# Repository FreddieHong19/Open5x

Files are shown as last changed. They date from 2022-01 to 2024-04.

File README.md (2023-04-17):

# Introduction

Democratising 5-axis 3D printing

At present, many people are unable to access 5-axis 3D printing due to the unavailability of hardware and software for personal use. Commercial multi-axis CNC machines and robotic arms are not designed specifically for additive manufacturing, and their firmware does not support standard 3D printing functions. Moreover, even the most affordable 5-axis machine still costs more than $9,945, which makes it prohibitively expensive for personal use. 

On the other hand, community engagement has been the primary driving force behind the widespread adoption of 3D printing in various industries. Through collaborative development, 3D printers have become more affordable, functional, and user-friendly. Similarly, 5-axis 3D printing could also benefit from the open-source community to accelerate its development and growth.

Open5x is a project that draws inspiration from open-source machines for personal fabrication. The project demonstrates how a popular off-the-shelf 3-axis 3D printer can be upgraded to 5-axis 3D printing, enabling more independent makers to take advantage of the benefits of conformal 3D printing.

The Open5x project was first showcased at the 13th Annual Conference on Human Computer Interaction Design and Research, and since then, has been demonstrated at various make fairs and 3D printing events such as 3D meetup Sweden, ERRF, and FormNext supported by Duet3D.

Related article:

https://dl.acm.org/doi/10.1145/3491101.3519782
https://doi.org/10.1016/j.addma.2023.103546

Link to the video:
https://youtu.be/x9rG15qrDIE

# Update

So far, Open5x hardware has been iterated and implemented onto various FDM 3D printers such as Prusai3, Voron and E3D's toolchanger system.
This conversion system requires some of the off-the-shelf components and 3D-printed parts. All of the necessary parts are listed in this repository.

The latest iteration of Open5X is running on E3D's toolchanger and Voron, developed by @BrendonBuilds 

-------

## License
The contents of this repository is under an MIT License, see [LICENSE.md](https://github.com/FreddieHong19/Open5x/blob/main/LICENSE) for more details.

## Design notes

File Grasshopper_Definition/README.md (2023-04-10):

# Usage

This folder contains the necessary files for using Grasshopper to create a 5-axis G-code.
Grasshopper is a visual scripting extension integrated into a popular 3D CAD software called Rhino 3D.
Unfortunately, Rhino 3D is not free software, but a 90 days fully functioning free-trial version is provided.

The grasshopper script here is still undergoing improvement and development.
The eventual goal is to migrate the system off Rhino 3D and operate somewhere free and open source. 

The current iteration of the Grasshopper script requires the below dependencies:

https://www.food4rhino.com/en/app/heteroptera : To find a centroid of a 3D geometry
https://docs.microsoft.com/en-us/dotnet/api/system.linq?view=net-6.0 : To collect max/min values in list

Rhino 3D and Grasshopper are excellent for simulating the movements of the hardware.
To simulate the movement, the 3D file of the rotary gantry (e.g. Prusa_5axis_profile_v2.3dm) needs to be uploaded inside the simulation node.

# Update

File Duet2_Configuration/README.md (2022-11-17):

For Prusa i3 MK3s 5-axis conversion Duet2 Wifi or Duet2 Ethernet can be used.
Two add extra two stepper motors for axis 'U' and 'V' Duex5 expansion board is required.
Please see the documents below for setting up the Duet2 board and Duex5 expansion for the first time.

https://docs.duet3d.com/en/How_to_guides/Getting_connected/Getting_connected_to_your_Duet

https://docs.duet3d.com/en/Duet3D_hardware/Duet_2_family/DueX2_and_DueX5

The steps-per-mm need to be adjusted depending on the gear-ratio, microstepping, stepper motor specs that you choose.
It would be advised to move the axis (especially U and V) at small incremental steps and assess that angle after.

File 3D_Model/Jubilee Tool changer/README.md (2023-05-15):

# Jubilee 3D Printer Open5x Implementation

This is a work-in-progress folder for files associated with creating an Open5X Jubilee 3D Printer. The files are provided, as-is, with no implied further support. Fabricating the module is easy but there is inherent risk with its use; collisions or other issues could cause permanent mechanical damage. Use at your own risk.

The files in this folder have been tested on a 300 mm^3 build space Jubilee 3D printer and may require modification for production systems.

# Introduction
These files are for modifying a Jubilee 3D printer to be compatible with the 5-axis build platform in the E3D_ToolChanger folder in this repo. By printing and assembling these parts, the Z-axis on a stock Jubilee can accept the existing 5-axis build platform.

# Integration Warnings
- Make sure to set tool change macros such that the tool will always clear the top of the 5-axis build platform before and after tool changes
- Collisions of the build plate and the gantry can happen during 5-axis printing. Be careful!

# Hardware Required
The below hardware is in addition to the additional hardware needed to make the 5-axis build platform specified in the E3D_Toolchanger folder

## Components to affix metal plate to z-axis couplers
(You can re-use the existing nuts and bolts below from your current Z-axis bed couplers if needed)
- 8x bolts to affix to linear rails
- 2x anti-backlash nuts for Z-axis travel
- 8x M4 heat-set inserts to affix to Z-axis bridge plate (Recommend Ultrasert ii)
- 8x M4 bolts to affix to Z-axis bridge plate
  
## Components to affix the 5-axis build platform to the Z-axis bridge plate
- 4x M4 bolts
- 4x M4 nuts

# Printed Parts
- 1x left bed coupler
- 1x right bed coupler

# Additional Parts
The below part can be ordered from sendcutsend or another laser cutting service (should be ~$35 total, shipped).

- 1x Z-axis bridge plate

# Firmware Notes
- A Duet3 with RepRap Firmware was used.
- An example config file is provided for you to adapt to your printer. Make sure to use the file as an example only to adapt to your own use case and printer setup.

# Additional Notes
- (A axis would rotate around the X-axis by convention)
- B axis rotates around the Y-axis by convention
- C axis rotates around the Z-axis by convention

# Potential Improvements for Next Revision
- Use 20x40 AL extrusion instead of laser-cut steel, add additional printed component in this design
- Explain changes to config vs. stock and add additional documentation

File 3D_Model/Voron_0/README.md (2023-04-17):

# Voron 0 Open5x Implementation

This is a work-in-progress folder for files associated with creating an Open5X Voron 0. The files are provided, as-is, with no implied further support. Fabricating the module is easy but there is inherent risk with its use; collisions or other issues could cause permanent mechanical damage. Use at your own risk.

The files included in this folder have been tested on a Voron v0.1 and may require modification for other versions.

Requires:
- Standard Open5x components
- 1 x 208mm 2GT belt
- 1 x 220mm 2GT belt
- 2 x NEMA17, 30mm body stepper motors (27mm preferred for B axis)
- 1 x 80-teeth, 2GT, 10mm bore pulley
- 1 x 10mm-diameter shaft, 70mm long
- 2 x Flanged Sleeve Bearing (McMaster 6659K118)
- 1 x 10mm Universal Mounting Hub
- M3/M4 Heat Set Inserts
- M3/M4/M5 Fasteners



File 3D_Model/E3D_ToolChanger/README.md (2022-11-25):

# E3D ToolChanger Open5x Implementation

This is a work-in-progress folder for files associated with creating an Open5X ToolChanger. The files are provided, as-is, with no implied further support. Fabricating the module is easy but there is inherent risk with its use; collisions or other issues could cause permanent mechanical damage. Use at your own risk.

The files included in this folder have been tested on an E3D Beta30 ToolChanger and may require modification for production systems.

Requires:
- Standard Open5x components
- 1 x 200mm 2GT belt
- 1 x 280mm 2GT belt
- 2 x NEMA17, 38mm body stepper motors
- 1 x 80-teeth, 2GT, 10mm bore pulley
- 1 x 10mm-diameter shaft, 72mm long
- 2 x Flanged Sleeve Bearing (McMaster 6659K118)
- 1 x 10mm Universal Mounting Hub
- M3/M4 Heat Set Inserts
- M3/M4 Fasteners

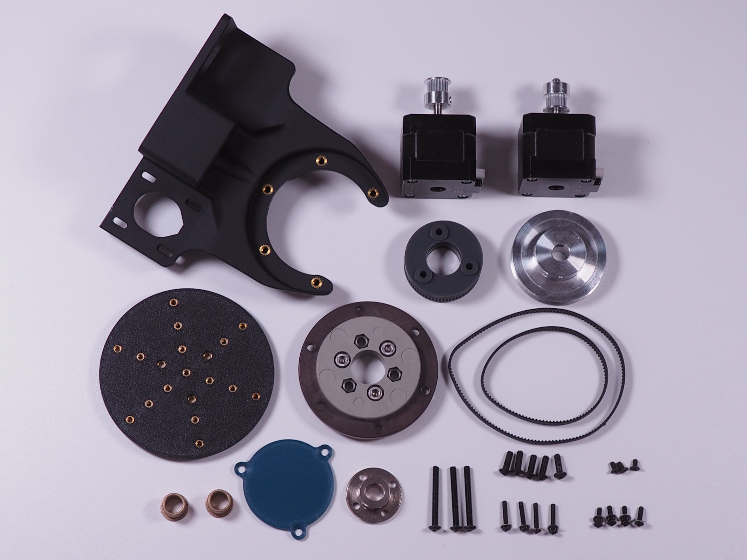
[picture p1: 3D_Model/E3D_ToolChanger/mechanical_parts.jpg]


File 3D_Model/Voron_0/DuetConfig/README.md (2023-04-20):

# These files are extremely specific to the prototype machine and should only be used as a reference.

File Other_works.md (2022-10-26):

There are several multi-axis 3D printing projects by various researchers with different approaches.
Please use pull request to add your or other project that are related

| Name  | Researcher | Link |
| ---|--|--|
| XYZdims | Rene K. Muller  | https://xyzdims.com/2021/02/08/3d-printing-penta-axis-pax-5-axis-printing-option/ |
| Aligning Material Extrusion Direction with Mechanical Stress via 5-Axis Tool Paths |Gardner et al.  | https://repository.lboro.ac.uk/articles/conference_contribution/Aligning_material_extrusion_direction_with_mechanical_stress_via_5-axis_tool_paths/9339410 |
| Reinforced FDM: Multi-Axis Filament Alignment with Controlled Anisotropic Strength | Fang et al.  | https://dl.acm.org/doi/abs/10.1145/3414685.3417834 |
| Five-axis additive manufacturing of freeform models through buildup of transition layers | Isa et al. | https://www.sciencedirect.com/science/article/pii/S0278612518301419?via%3Dihub |
|Marlin2ForPipetBot | HendrickJan | https://github.com/DerAndere1/Marlin/tree/Marlin2ForPipetBot/config/examples/multi_axis_3D_printer/HendrikJan-5D|

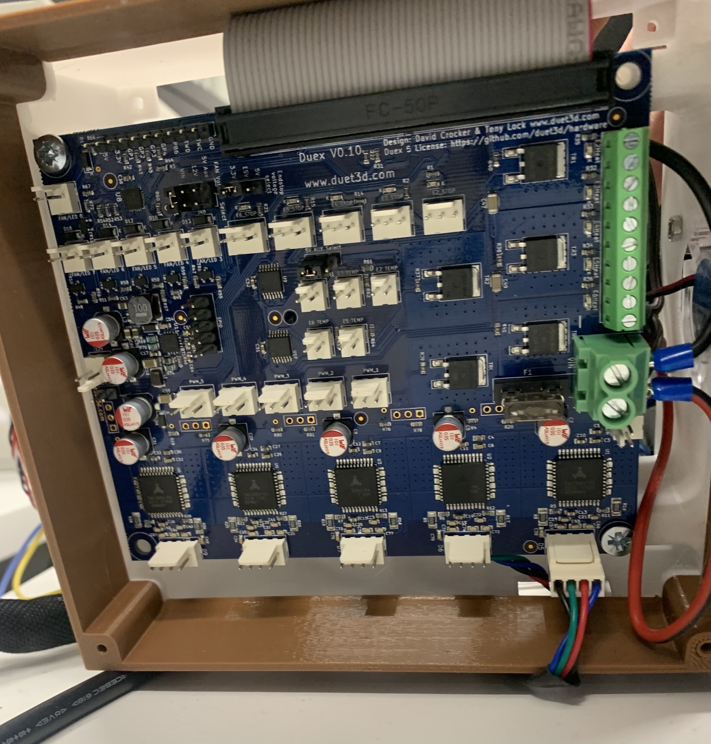
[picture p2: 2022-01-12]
images/Duex5.jpg

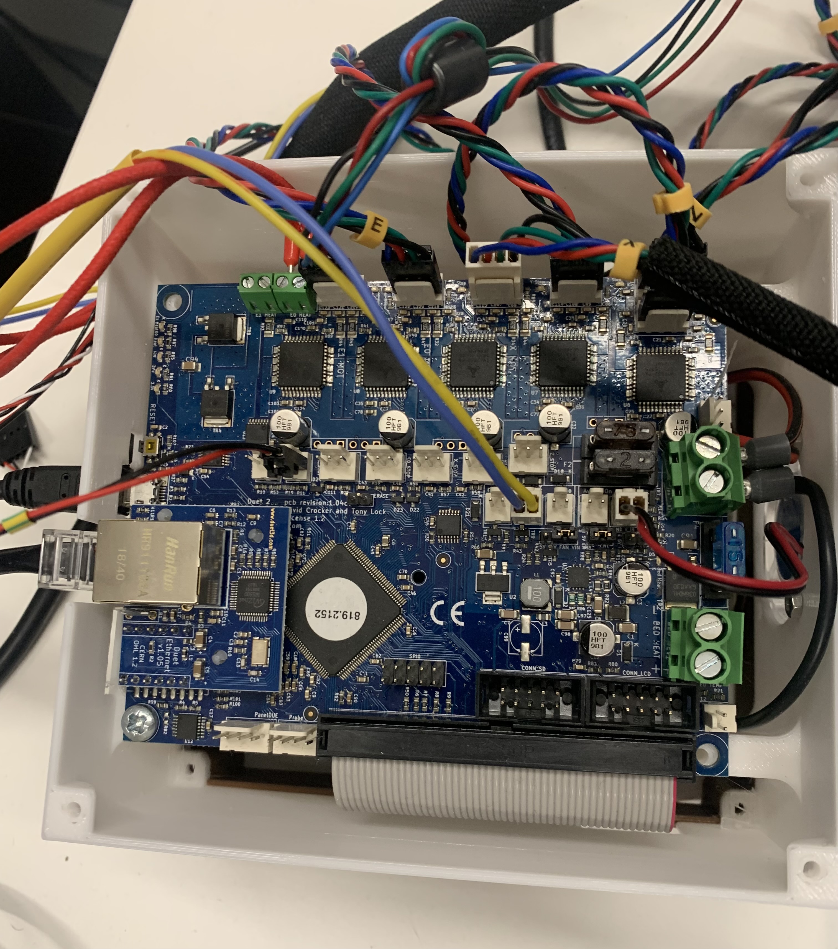
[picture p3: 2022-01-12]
images/Duet2.jpg

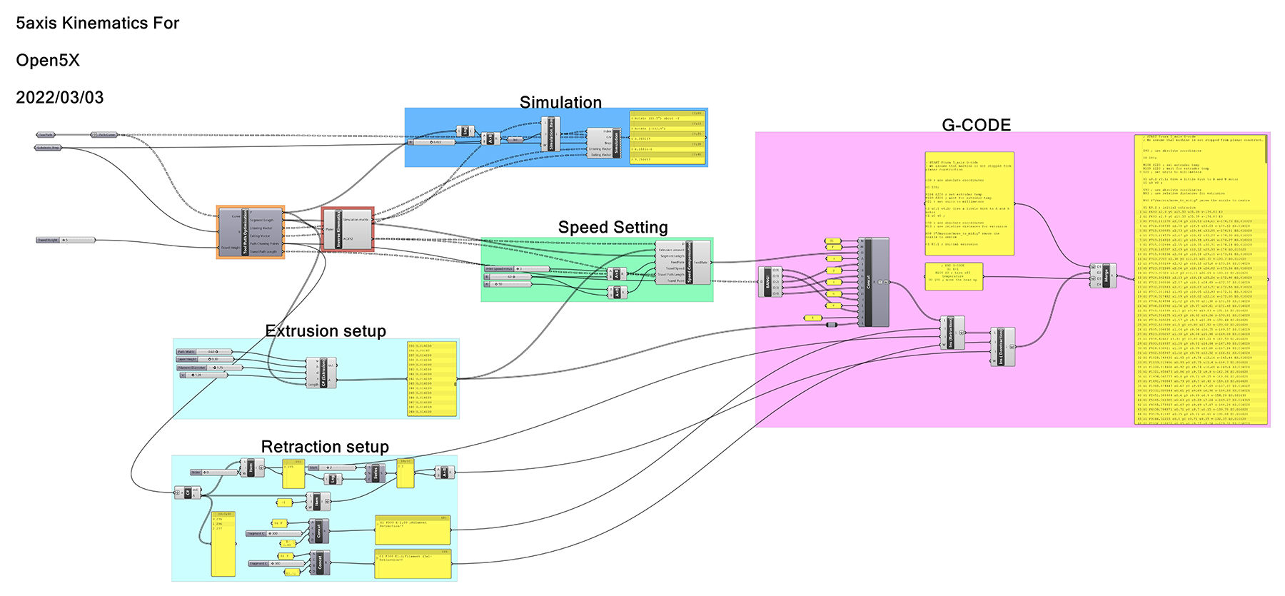
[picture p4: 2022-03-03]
images/grasshoper_main.jpg

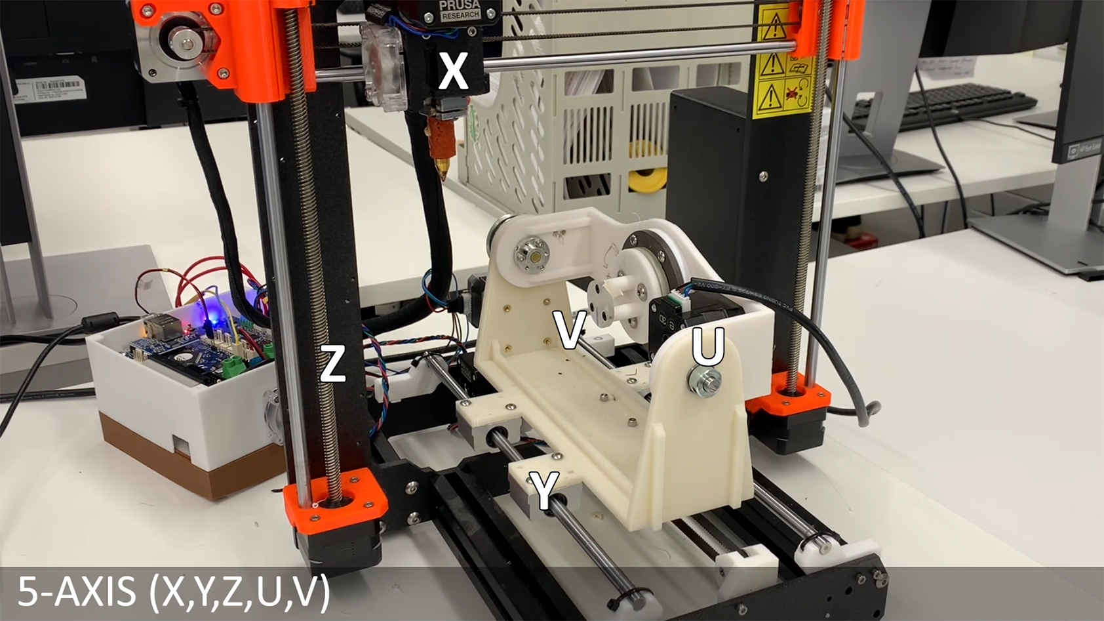
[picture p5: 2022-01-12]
images/5_axis_Prusa.jpg

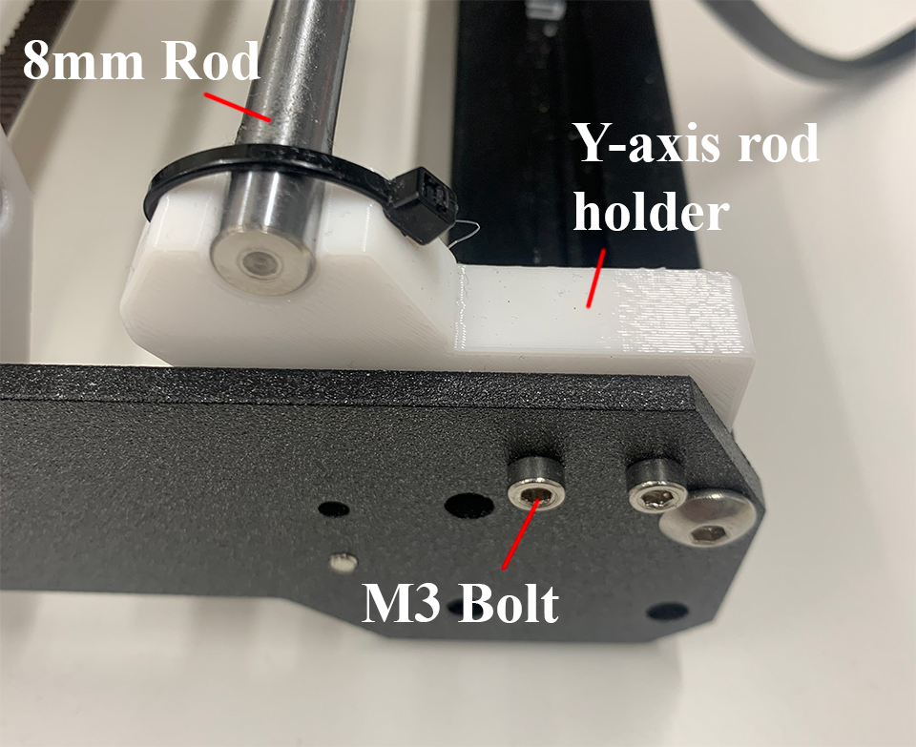
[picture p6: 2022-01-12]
images/Y_axis_rod.jpg

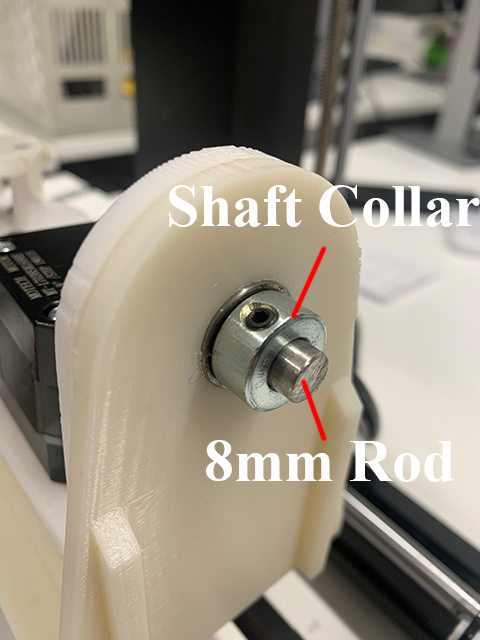
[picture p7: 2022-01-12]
images/U_axis_shaft.jpg

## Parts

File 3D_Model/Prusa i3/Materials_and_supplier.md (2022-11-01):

This a list of materials and suppliers used for converting Prusa i3 to 5-axis 3D printer

| Name  | Supplier | Link |
| ---|--|--|
| 0.9 deg NEMA 17 Compact Stepper Motor x 2 | E3D, UK  | https://e3d-online.com/products/motors |
| GT2 60 Pulley x2 8mm bore  | RepRap World, UK  | https://reprapworld.co.uk/ |
| GT2 20 Pulley x2 5mm bore for stepper motor shaft | RepRap World, UK | https://reprapworld.co.uk/ |
| 200-GT2 Belt x1 | Amazon, UK | www.amazon.co.uk/ |
| 224-GT2 Belt x1 | Odroid, UK | https://www.odroid.co.uk/index.php?route=product/product&product_id=902&search=GT2 |
| D:8mm L:35mm  Steel dowel x2 | Amazon, UK | www.amazon.co.uk/ |
| 8mm Flange Bearing x2 F6882RS | SimplyBearings, UK | https://simplybearings.co.uk/shop/ |
| 8mm shaft collar | RS Online, UK | https://uk.rs-online.com/web/ |
| Linear Bearing Slider Blocks SC8UU | Ooznest, UK | https://ooznest.co.uk/product/linear-bearing-slider-blocks/ |
| Slewing ring bearing | Igus, UK | https://www.igus.co.uk/product/661?artNr=PRT-02-20-LC |
| Duet 3 Mini 5+ | Duet3D, UK | https://duet3d.com/duet3mini5plus |
| Duet 3 Mini 2+ | Duet3D, UK | https://duet3d.com/duet3expansionmini2plus|
| (alternative to mini 5+) Duet2 Wifi | Duet3D, UK | https://www.duet3d.com/DuetWifi |
| (alternative with Duet 2 Wifi) Duex5 | Duet3D , UK | https://www.duet3d.com/Duex5 |
| Universal 8mm Pololu mounting hub| PIMORONI , UK | https://shop.pimoroni.com/ |
| Long Brass Nozzle 0.4mm | nonplanar.xyz, CANADA | https://www.nonplanar.xyz/product-page/0-4mm-non-planar-nozzle |
| M3_8mm Hex Bolt x14 (Polou mounting hub, Nema motors)| Accu, UK | www.accu.co.uk |
| M3_12mm Hex Bolt x2 (Y-axis Belt_holder)| Accu, UK | www.accu.co.uk |
| M4_14mm flat Bolt x8 (SC8UU)| Accu, UK | www.accu.co.uk |
| M4_20mm flat Bolt x8 (slewing ring)| Accu, UK | www.accu.co.uk |
| M5_25mm flat Bolt x3 (slewing ring)| Accu, UK | www.accu.co.uk |
| M3_lock nut x2 (Y-axis Belt_holder | Accu, UK | www.accu.co.uk |
| M5 nut x3 (slewing ring) | Accu, UK | www.accu.co.uk |
| M4 nut x8 (slewing ring) | Accu, UK | www.accu.co.uk |
| M3x4x5 Threaded inserts x10| Amazon, UK | www.amazon.co.uk |

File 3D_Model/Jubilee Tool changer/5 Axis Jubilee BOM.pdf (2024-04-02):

# 5 Axis Jubilee BOM

## Tools:

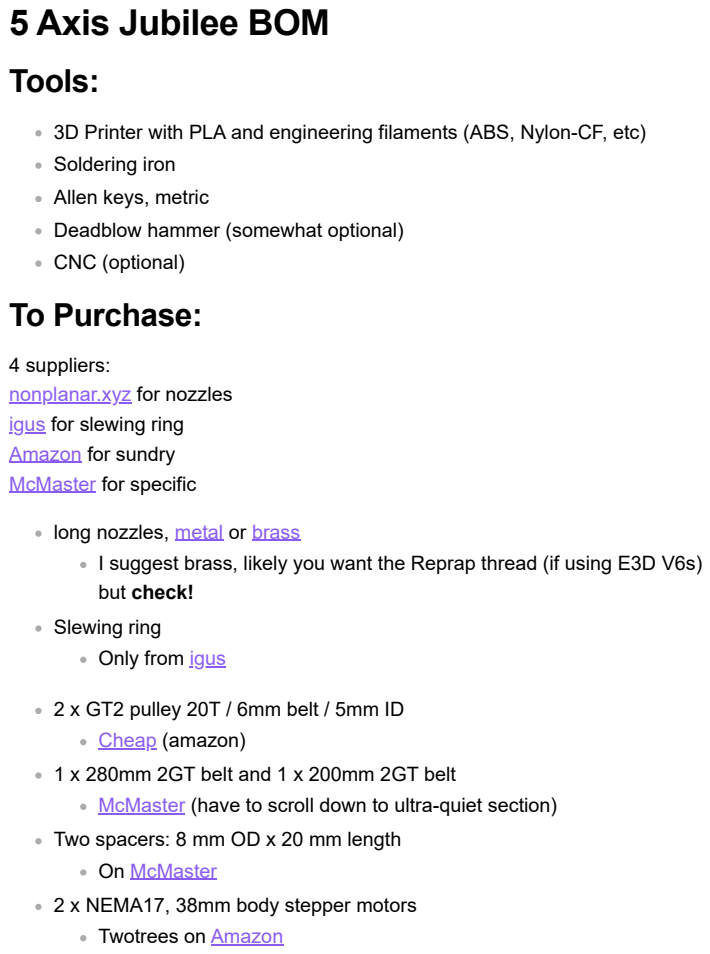
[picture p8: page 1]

3D Printer with PLA and engineering filaments (ABS, Nylon-CF, etc)
Soldering iron
Allen keys, metric
Deadblow hammer (somewhat optional)
CNC (optional)
To Purchase:

4 suppliers:
nonplanar.xyz for nozzles
igus (https://www.igus.com/) for slewing ring
Amazon (https://www.amazon.com/) for sundry
McMaster (https://www.mcmaster.com/) for specific

long nozzles, metal (https://www.nonplanar.xyz/product-page/5-all-metal-nozzle-0-4mm) or brass (https://www.nonplanar.xyz/product-page/5-reprap-brass-nozzle-0-4mm)
I suggest brass, likely you want the Reprap thread (if using E3D V6s)
but check!
Slewing ring
Only from igus (https://www.igus.com/product/661?artNr=PRT-02-20-LC)

2 x GT2 pulley 20T / 6mm belt / 5mm ID
Cheap (https://www.amazon.com/WINSINN-Aluminum-Synchronous-Timing-Printer/dp/B077GNZK3J) (amazon)
1 x 280mm 2GT belt and 1 x 200mm 2GT belt
McMaster (https://www.mcmaster.com/products/powergrip-timing-belts/) (have to scroll down to ultra-quiet section)
Two spacers: 8 mm OD x 20 mm length
On McMaster (https://www.mcmaster.com/products/spacers/spacers~/system-of-measurement~metric/od~8-000-mm/od~8-0-mm/od~8-mm/length~20-mm/screw-size~m3/)
2 x NEMA17, 38mm body stepper motors
Twotrees on Amazon (https://www.amazon.com/Twotrees-Stepper-17HS4401-Connector-Printer/dp/B07TGJT5M2)

## To Print

Print in rigid engineering filaments that can take some beating. I used Markforged ABS / Fiberglass reinforced. These parts are from Garth42's Jubilee-Open5x-assembly.step on the Open5x Github: (https://github.com/FreddieHong19/Open5x/tree/main/3D_Model/Jubilee%20Tool%20changer)

## To Machine

Can use a service like sendcutsend or cut on any CNC available to you -- it is a very simple, flat piece, and any type of metal 1/8" or thicker should do.

## Nuts and Bolts

1 x 80-teeth, 2GT, 10mm bore pulley $11.50 for 1x on Amazon (https://www.amazon.com/MECCANIXITY-Aluminium-Synchronous-Printer-Machine/dp/B0BK4VXTZC)
$17 for 2x and random stuff on Amazon (https://www.amazon.com/Befenybay-Synchronous-Aluminum-Timing-20-80T-10B-6/dp/B09YSR1TBF)
1 x 10mm-diameter shaft, 72mm long
Amazon (https://www.amazon.com/10mm-300mm-Vigorous-Hardened-Printer/dp/B0BZQ7T7JJ)
2 x Flanged Sleeve Bearing (McMaster 6659K118) Link (https://www.mcmaster.com/catalog/129/1412/6659K118)
1 x 10mm Universal Mounting Hub
- $10 but more reviews here (https://www.amazon.com/Coupling-Connector-Coupler-Accessory-Fittings/dp/B08334DK91)
- $6.50 but less reviews here (https://www.amazon.com/Cionyce-Coupling-Support-Hardness-Connector/dp/B0B63PGGZR)
Budget: parts about should run about $175. Depending on the cost of machining and which filament used in printing, below $300 is reasonable.

Main body
100 mm bed
1x left bed coupler
1x right bed coupler
Wiring holder
72T shorter c-gear (can be printed in SLA)

Z-axis bridge plate


(from Brendon Build's mechanical-parts.jpg (https://github.com/FreddieHong19/Open5x/tree/main/3D_Model/E3D_ToolChanger) on the Open5x Github)

8x bolts to affix to linear rails (M3 I think) 8x M4 bolts to affix to Z-axis bridge plate 4x M4 bolts
4x M4 nuts
M3/M4 Heat Set Inserts
M3/M4 Fasteners

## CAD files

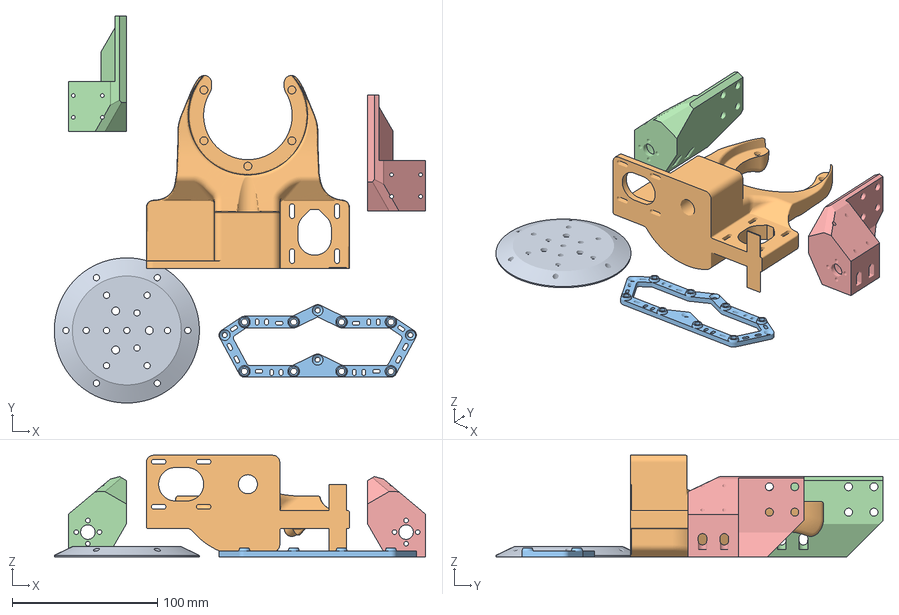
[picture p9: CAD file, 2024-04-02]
3D_Model/Jubilee Tool changer/Open5x Assembly Oriented Print Parts.3mf
256.0 x 266.7 x 70.0 mm
100mm-bed v3.step
Jubilee-Open5x-assembly_1
Tool Board Holder.step
Left Bed Coupler (Jubilee).STL
Right Bed Coupler (Jubilee).STL

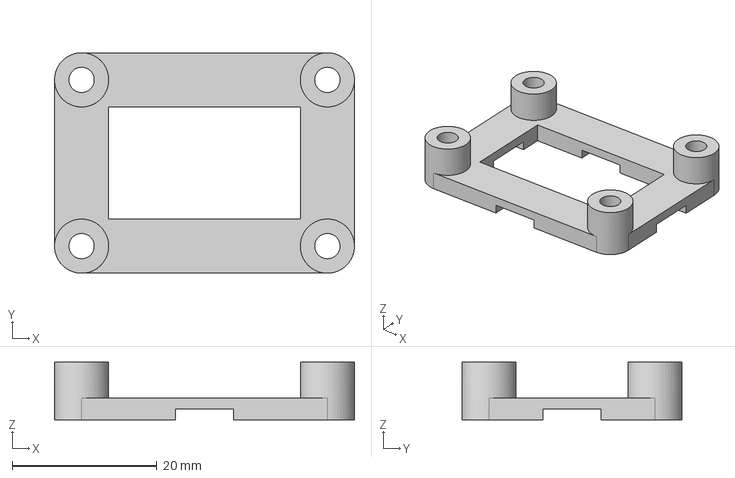
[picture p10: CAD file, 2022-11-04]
3D_Model/modifications/toolboard_23mm_bracket.step
41.5 x 30.5 x 8.00 mm

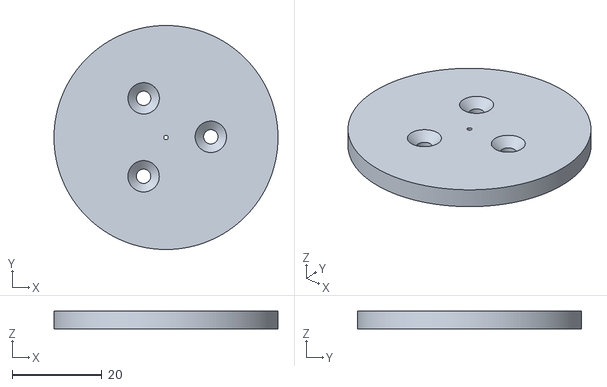
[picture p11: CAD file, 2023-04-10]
3D_Model/Prusa i3/Printbed_50mm v1.stl
50.0 x 50.0 x 4.00

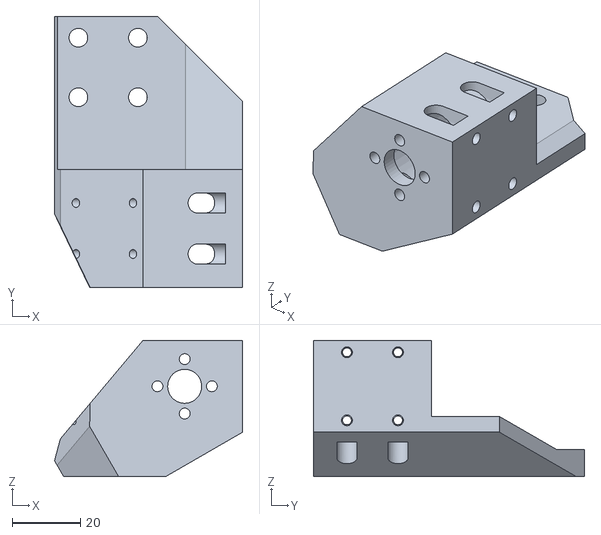
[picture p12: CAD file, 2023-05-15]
3D_Model/Jubilee Tool changer/Right Bed Coupler.STL
55.3 x 79.7 x 40.0

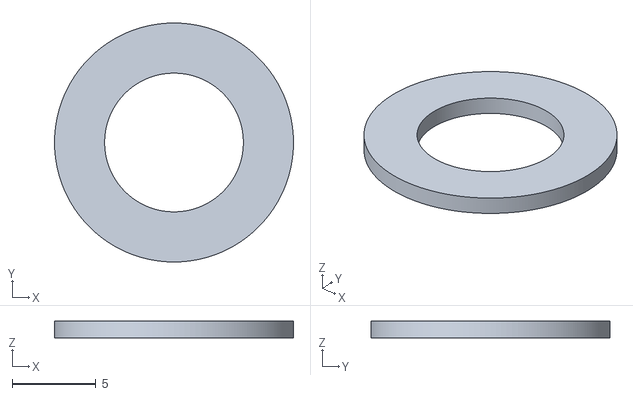
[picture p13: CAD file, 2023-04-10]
3D_Model/Prusa i3/U-axis_1mm_spacer.stl
14.3 x 14.3 x 1.00

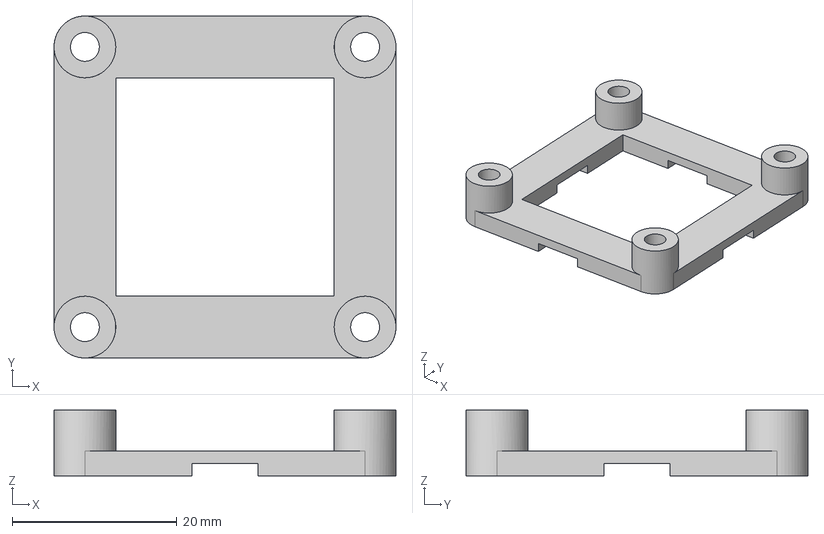
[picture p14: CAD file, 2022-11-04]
3D_Model/modifications/toolboard_34mm_bracket.step
41.5 x 41.5 x 8.00 mm

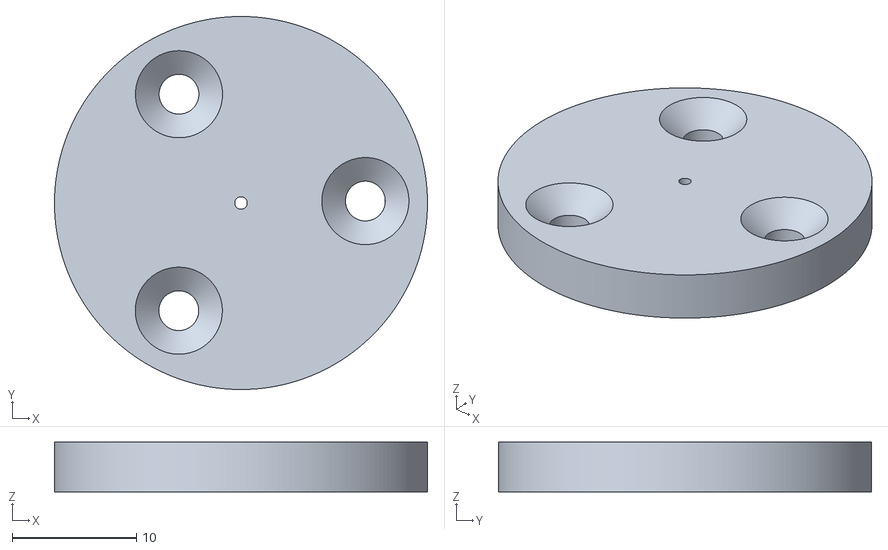
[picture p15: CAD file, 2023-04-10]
3D_Model/Prusa i3/Printbed_30mm v3.stl
30.0 x 30.0 x 4.00

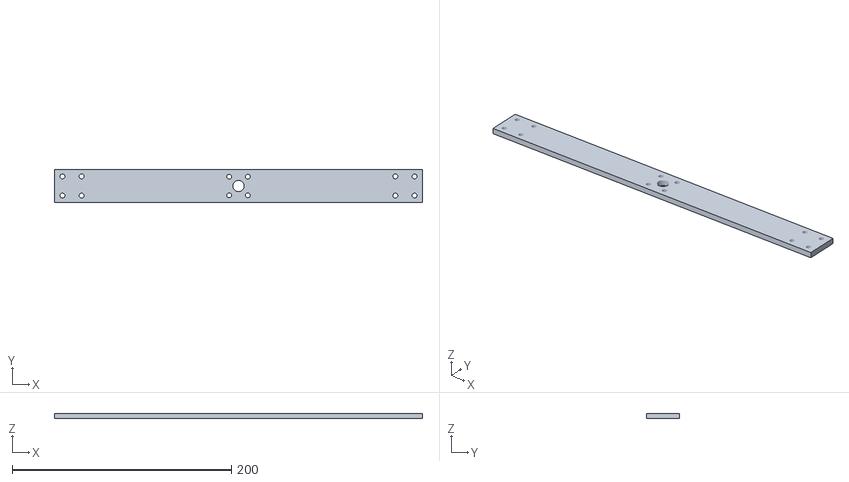
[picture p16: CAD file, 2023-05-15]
3D_Model/Jubilee Tool changer/Z-axis Bridge Plate.STL
336.0 x 30.0 x 5.00

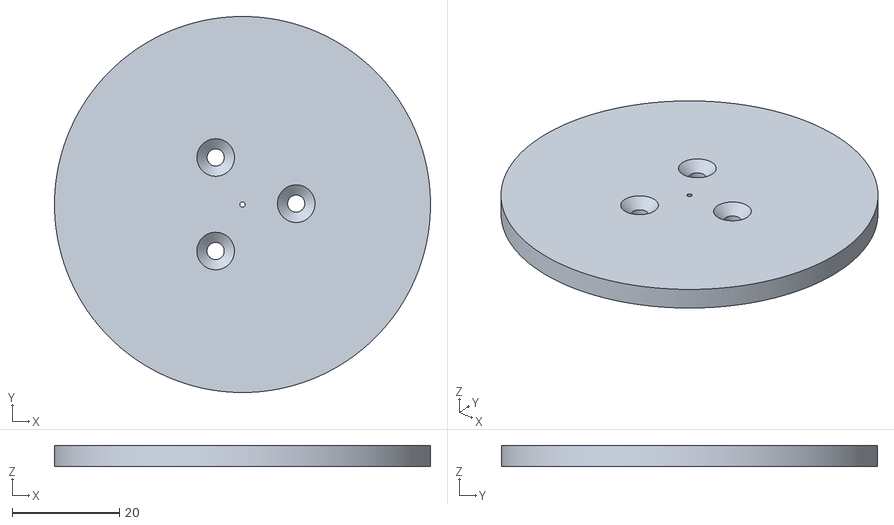
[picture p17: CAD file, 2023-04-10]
3D_Model/Prusa i3/Printbed_70mm v3.stl
70.0 x 70.0 x 4.00

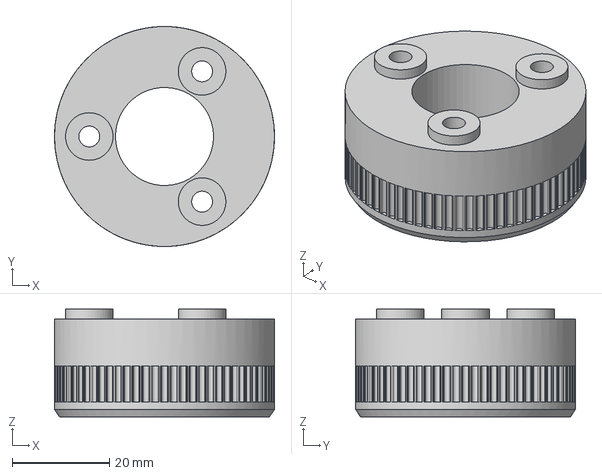
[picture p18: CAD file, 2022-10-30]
3D_Model/modifications/V_axis_pulley_72t_resin.step
45.3 x 45.3 x 22.2 mm

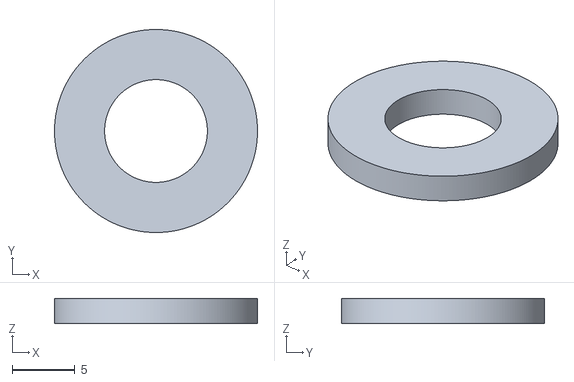
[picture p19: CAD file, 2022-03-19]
3D_Model/Prusa i3/U_axis_2mm_spacer.stl
16.2 x 16.2 x 2.00

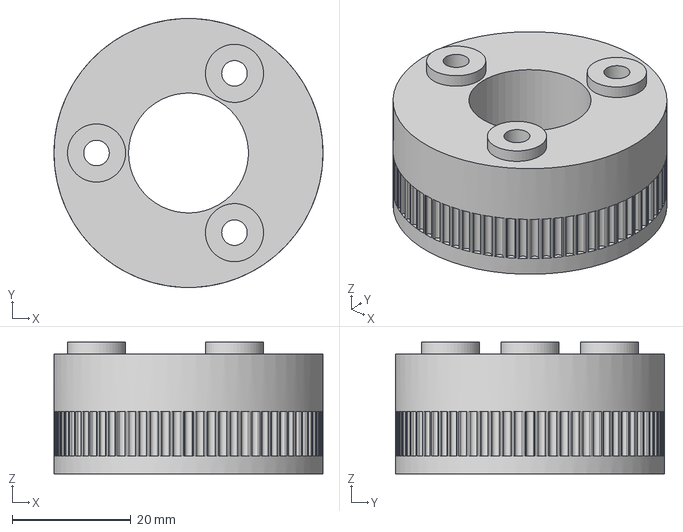
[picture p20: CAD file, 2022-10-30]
3D_Model/modifications/V_axis_pulley_72t_fdm.step
45.3 x 45.3 x 22.2 mm

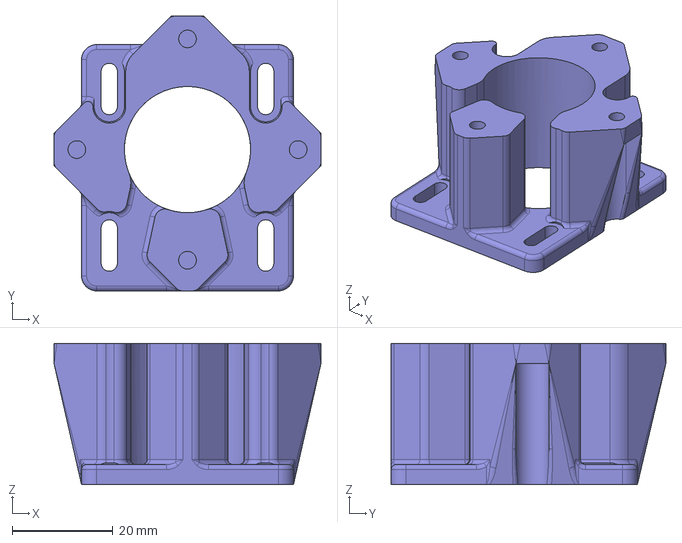
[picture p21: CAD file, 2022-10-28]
3D_Model/modifications/U_axis_motor_mount_28mm.step
52.9 x 54.4 x 28.0 mm

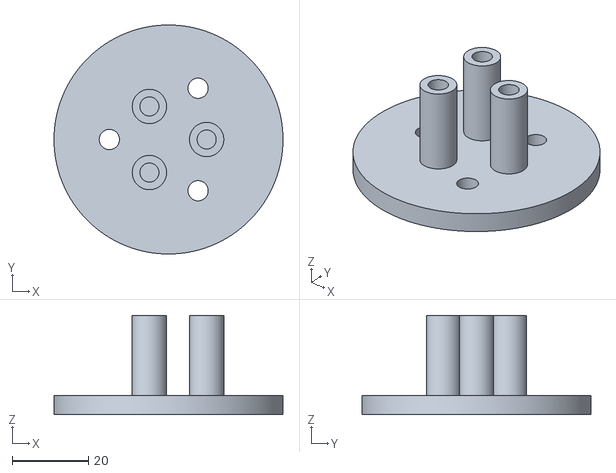
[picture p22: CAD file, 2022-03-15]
3D_Model/Prusa i3/Print_bed_support_70mm.stl
60.0 x 60.0 x 26.0

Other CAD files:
3D_Model/Jubilee Tool changer/Left Bed Coupler.STL
3D_Model/modifications/U_axis_motor_mount_22mm.step
3D_Model/Prusa i3/Y_axis_motor_mount.stl
3D_Model/Prusa i3/Y_axis_bearing_holder.stl
3D_Model/Prusa i3/Printbed_30mm v1.stl
3D_Model/Prusa i3/Slewing_ring_adaptor.stl
3D_Model/Prusa i3/U_axis_motor_mount.stl
3D_Model/Prusa i3/V_axis_carriage.stl
3D_Model/Prusa i3/V_axis_shaft_hub.stl
3D_Model/Prusa i3/Y_axis_8mm_rod_holder.stl
3D_Model/Prusa i3/Y_axis_carriage.stl
3D_Model/modifications/V_axis_carriage_4_bolt.step
3D_Model/modifications/V_axis_carriage_6_bolt.step
Grasshopper_Definition/Supportless_sample_2.3dm

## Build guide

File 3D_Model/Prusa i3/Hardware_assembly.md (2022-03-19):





Exploded Isometric image of the gantry assembly



8mm Rod fixed onto the Prusai3 frame



8mm Dowel connection on V_axis_carriage

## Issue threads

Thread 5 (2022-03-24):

Consider porting to BTT GTR

pyr0ball, 2022-03-24:
It seems TeamGloomy have gotten a decent port of RRF to work on these cheaper GTR boards. Would you be willing to consider building a version specific to that setup, or assist me in porting it?

I plan on re-engineering this project for an old FlashForge Creator Pro, and happen to have one of these GTR's on hand to work with

https://teamgloomy.github.io/gtr_pins.html

Keybored02, 2022-03-30:
I second this. The BTT GTR, SKR (with the 3axis expansion module), and Octopus are extremely widespread among makers. The Duet boards, given the cost, are more for prosumers. A Marlin port would also be a great improvement, given how 2.0.9 has simplified the addition of more (linear) axis.

FreddieHong19, 2022-03-31:
Hi,
Thank you for sharing this information about your GTR board suggestion! I will have a read through their documentation and see if it could be implemented. Personally for now, I am very satisfied with Duet board especially regarding their hardware, expandability and their web controller. I

pyr0ball, 2022-03-31:
If I had to choose between the two and price was no object, (or if I had one on hand myself) I'd probably feel the same!

Do you think if I simply used the configs from this project on the existing RRF fork for the GTR, it might just work? I'd be happy to give it a shot if so. If there's any obvious pitfalls with that method, and you could point them out ahead of time, I'd be happy to do the legwork on investigation and testing

Closed 2022-10-18.

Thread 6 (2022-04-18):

7Axis 5D Printer

HendrikJan-5D, 2022-04-18:
In response to your nice Open5x project and the question
(( We want to have more hobbyists and makers on board with 5-axis 3D printing. ))
This response.

I am new to this forum.
As a member of 3d.hcc.nl , a hobby club of members who are involved in 3d printing, 3d scanning, cad software (fusion 360).
I am involved in technical support and new developments in the 3d field.
In the context of this I have built a 5d printer
This can be done by turning and tilting the print head, or by turning and tilting the bed.
Because I couldn't choose the best method, I decoder to build both in the 3d printer, which results in a 5d printer with 7 axes.

See : https://youtu.be/pjuG15b2zaI

Further information can be found at:

My 5D printer configuration Marlin
https://github.com/DerAndere1/Marlin/tree/Marlin2ForPipetBot/config/examples/multi_axis_3D_printer/HendrikJan-5D

Wiki DerAndere1
https://github.com/DerAndere1/Marlin/wiki

Test reports 9 Axis configuration
https://github.com/DerAndere1/Marlin/issues/55

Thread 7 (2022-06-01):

Question about model slicing

Shuwrood-SSW, 2022-06-01:
Thanks for sharing your great works, but I still have no idea much about the slicing software.
For examole, when I use the model of Supportless_sample_2 (small fan), the otary bearing can't be fixed and positioned. I would appreciate a detail video tutorial  about slicing if you could.  Moreover,  can you upload the model of the spiral staircase used in your video for better. Thank you very much.

FreddieHong19, 2022-06-05:
Hi Shuwrood,

From your screenshot it appears that the model which you are importing is not at 0,0,0 coordinates. If you position the bottom face of the model, the slicing preview may appear at the right location.
I am going through iterations of development to create a stable version of the slicer +I am planning more detailed video tutorials. I am hoping to share them in a nearer time, but it is taking longer than I have anticipated!
Best,

Shuwrood-SSW, 2022-06-06:
That's really great. Looking forward to the video tutorial! Besides, could you upload the following model to github.

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

syalways, 2022-07-14:
sorry,I have a question that this model can not  print in_fill lite,is itright?

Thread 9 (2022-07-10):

How to determine the Z_Axis edge of irregular multifax surfaces

syalways, 2022-07-10:
There is a question I would like to ask, like this kind of irregular multiple surfaces how to determine which is the z-axis edge, I tried several directions, but the resulting path is not right.can you help answer it, thank you very much.
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

xuanxuanbingo, 2023-03-21:
Hello, I want to ask have you successfully reappear the whole process on the grasshopper?

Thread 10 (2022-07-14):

in_fill

syalways, 2022-07-14:
sorry,I have a question that this model can not  print in_fill lite,is it right?

FreddieHong19, 2022-10-18:
I am not too clear on what you mean. If you are referring to the auto-generating infill pattern, then the current version I am sharing is not supporting this.

Closed 2022-10-18.

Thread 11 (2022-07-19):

Help

dongqi0101, 2022-07-19:
Thanks for your work! Currently I'm trying to fork your work, but I'm having a lot of problems and really need your help.
1. Can you upload the original version of your GH (not a simplified version)
2. How did the direct printing on the sphere shown in your video work? Can the GH you upload achieve this effect?
3. I have a model here, can you help me try it? I hope to use the hemisphere as the support, and only print the pattern on the sphere. I have tried many times by myself, but all failed.
I am very interested in your work, I find it very valuable and I really need your help
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
[模型调整.zip](https://github.com/FreddieHong19/Open5x/files/9137614/default.zip)
If possible, this is my mailbox (1241153590@qq.com), looking forward to hearing from you

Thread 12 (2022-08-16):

no issue - just congrat

vivi3n, 2022-08-16:
Hello, I tested your gh code because I was so excited to understand how you created the g-code for the 5_axis machine ^^ Actually, it seems relatively (hopelessly) easy and thanks again for sharing your code and l simulation tool works so well! I will try to reproduce the Prusa too. I hope to find the time for that. Thanks again for your amazing work!

For my part I work on 3d print auxetic structure on rotative Y axis 3d printer. I hope with your project make a huge gap !

Best

Closed 2022-10-18.

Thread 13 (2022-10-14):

Can the Duet 3 mini 5+ and mini 2+ expansion board be used?

critter42, 2022-10-14:
I was looking at this project after Joel's video today and noticed I had most everything on hand to start on this. The only difference is I have the Duet 3 mini 5+ and the 2+ expansion board for it. It looks like this is all I need, since you're only using one driver on your Duet 2's expansion board. Am I correct on this?

FreddieHong19, 2022-10-18:
Hi critter42,

I believe that you are!
Your suggestion is probably a neater solution because you don't waste any extra stepper drivers!

T3P3, 2022-10-31:
yes, they are a good solution for this project!

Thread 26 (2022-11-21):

Mail

dongqi0101, 2022-11-21:
Your work is great, and I am also learning with it myself, but I have encountered many problems. Can you share your email address so that I can get your help more easily?

FreddieHong19, 2022-11-28:
Hello, Dongqi.

Could you please share the issue on repo? In case it might applies to other people who may want to use open5x?
Thank you!

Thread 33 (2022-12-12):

Make available for Mac Rhino Users

mikedattolo, 2022-12-12:
I use a mac and can not open the grasshopper file on Rhino because the plugin used to make the file is only useable on Windows machines. Is it possible to make this available in a way mac users can see and use it as well...

BigKoala33, 2022-12-14:
Hi @mikedattolo what is the name of that plugin?

BigKoala33, 2022-12-14:
Hi @mikedattolo what is the name of the plugin?

mikedattolo, 2022-12-15:
That's the problem. I'm not sure. I believe they are both Pufferfish and Heteroptera; however, I don't think it is a direct issue having to do with them. It has to do with something referenced in the grasshopper file here
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

mikedattolo, 2022-12-15:
And sorry again, I forgot that I am trying to use or make my own simulation through grasshopper to slice G-code for a 4-5 axis printer prototype I am working on for a class in college. It doesn't matter if I can't do it, but I would like to because I think this as a research subject/innovation for 3d printing would be amazing.

mikedattolo, 2022-12-16:
@BigKoala33

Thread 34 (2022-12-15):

How did you make your nozzle that long?

Page-David, 2022-12-15:
In your [video](https://www.youtube.com/watch?v=Sq2mH8-iBk8), the nozzle of hotend is obviously longer than a normal version of E3D v6 hotend. It looks like it is needed to avoid collision. So I am curious how did you make it? Is there somewhere it can be purchased?

Closed 2022-12-16.

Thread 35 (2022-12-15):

How did you make your nozzle that long?

Page-David, 2022-12-15:
In your [video](https://www.youtube.com/watch?v=Sq2mH8-iBk8), the nozzle of hotend is obviously longer than a normal version of E3D v6 hotend. It looks like it is needed to avoid collision. So I am curious how did you make it? Is there somewhere it can be purchased?

FreddieHong19, 2023-03-21:
Yes, If you check the material and supplier.md you will find the link

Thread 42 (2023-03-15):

PufferFish plugin not able to download

mikedattolo, 2023-03-15:
I try and open up the grasshopper file and I am able to download the first plugin no problem, However when it asks me to install pufferfish it fails, I have tried going to food4Rhino and manually downloading it but it doesn't acknowledge it and still asks me to download it and when I close out of the prompt I get a couple errors. At the same time I was wondering if this can be repurposed for other types of 5D printers ones that specifically uses rotational axis on the x-axis rather than the bed of the printer.

FreddieHong19, 2023-03-21:
Hi,
the grasshopper definition should still be functional without the pufferfish library. (Could you post a screenshot of an error)
The new version of the grasshoper definition will be shared soon during april!

mikedattolo, 2023-03-21:
> Hi, the grasshopper definition should still be functional without the pufferfish library. (Could you post a screenshot of an error) The new version of the grasshoper definition will be shared soon during april!

hey, thank you for responding. I figured it out. It was just because I had the pufferfish plugin block, and now it works, however I still am having issues with actually trying out the slicer, when I add in the brep and connect it to the supportless brep and substrate the slicer cant find the path curve that is connected to the conformal pathing cluster.

Closed 2023-03-24.

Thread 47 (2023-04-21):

How to Print

andybae, 2023-04-21:
Hi Freddie,

My project team built your 5-axis printer design. Still learning, but having trouble running your rhino and grasshopper files. We're using your open5x_suportless_slicing_ver2 grasshopper file and supportless_sample_2 rhino file. Is there anything we can do to fix this orange-colored error?

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

Also I understand that the grasshopper file produces that g-code output for 5d print instructions. We're kind of confused on what to do afterwards. Do we just copy this g-code into the prusa?

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

Also how did you calibrate the 5-axis printer to set initial coordinates before using the prior g-code to start printing?

Thank you

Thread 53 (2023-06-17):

using Russian 5D printer as a prototype

Divertisment, 2023-06-17:
I propose to use in development and steal and decompile what is not publicly available from this Russian 5d printer.
They have a successfully working and commercially available printer in two variants.
https://5dtech.pro/5d-530-fiber/

Here an open source slicer, it seems to me
https://github.com/stereotech/STE-Slicer

the control software (STE App) is a reworked fork the Cure to which they added a 5d processing module and made it proprietary (in violation of the license obviously)

sotnikovmisa, 2023-10-08:
how are the results?

sotnikovmisa, 2023-10-08:
It’s not easier to use a cracked Rhinoceros

vabka, 2023-11-10:
Let's violate license agreement of commercial software and use it's code in open source. What can go wrong? Lol

dimensionalcreations3d, 2023-11-14:
They want 18,500 USD for their fiber printer.

Seems like they're over estimating the value of what they built.

It's a cool machine, but there's enough open source gear out there to build one for far less.

Slicing is gonna be the main issue until it's "perfected".

That being said, I don't think stealing someone else's work is ever a good idea. It doesn't seem anything they have is proprietary (legally speaking) beyond their assertion that it is.

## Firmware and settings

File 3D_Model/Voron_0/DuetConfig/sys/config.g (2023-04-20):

; Configuration file for Duet 3 (firmware version 3)
; executed by the firmware on start-up
;
; generated by RepRapFirmware Configuration Tool v3.1.4 on Thu Oct 08 2020 13:25:03 GMT-0400 (Eastern Daylight Time)

; General preferences
G90                                          ; send absolute coordinates...
M83                                          ; ...but relative extruder moves
M550 P"Voron5x"                              ; set printer name
M669 K1                                      ; select CoreXY mode
M552 S1

; Network
M552 P0.0.0.0 S1                             ; enable network and acquire dynamic address via DHCP
M586 P0 S1                                   ; enable HTTP
M586 P1 S1                                   ; disable FTP
M586 P2 S0                                   ; disable Telnet

; Drives
M569 P0.0 S0                                 ; physical drive 0.0 goes forwards
M569 P0.1 S0                                 ; physical drive 0.1 goes forwards
M569 P0.2 S0                                 ; physical drive 0.2 goes forwards
M569 P0.3 S1                                 ; physical drive 0.3 goes backwards
M569 P0.4 S0                                 ; physical drive 0.4 goes forwards
M569 P0.5 S0                                 ; physical drive 0.5 goes forwards
M569 P0.6 S0                                 ; physical drive 0.6 goes forwards

M584 X0.6 Y0.5 Z0.0:0.4 B0.3 C0.2 E0.1            	  ; set drive mapping
M350 X16 Y16 Z16:16 B64 C64 E16 I1             		  ; configure microstepping with interpolation
M92 X80 Y80 Z1600:1600 B142.2222222 C128 E690    	  ; set steps per mm
M566 X1800 Y1800 Z360:360 B800 C800 E300     		  ; set maximum instantaneous speed changes (mm/min)
M203 X180000 Y180000 Z1200:1200 B61200 C61200 E7200   ; set maximum speeds (mm/min)
M201 X20000 Y20000 Z1000:1000 B2000 C2000 E3000       ; set accelerations (mm/s^2)
M906 X1500 Y1500 Z1200:1200 B1200 C1200 E1200 I30	  ; set motor currents (mA) and motor idle factor in per cent
M84 S30                                        		  ; Set idle timeout

M308 S1 P"temp0" Y"pt1000" L-25						        ; configure sensor 1 as heater core on pin temp0
M950 H1 C"out1" T1                          				; create nozzle heater output on out1 and map it to sensor 1
M307 H1 R2.027 K0.304:0.000 D5.15 E1.35 S1.00 B0 V23.7		; v6, duct, no part cooling, 24v/40w
M143 H1 S310												; max temperature of nozzle

M950 F1 C"out3"                              ; create a fan 1 on pin out3 and set its frequency
M106 P1 H1 T80                      	 	 ; set fan 1 value. Thermostatic control is turned on

; Axis Limits
M208 X-58 Y-58 Z-20 B-110 C-1000000 S1               ; set axis minima
M208 X115 Y115 Z85 B110 C1000000  S0                 ; set axis maxima

; Endstops
M574 X1 S3                                   ; configure sensorless homing for low end of x
M574 Y2 S3                                   ; configure sensorless homing for high end of Y
M574 Z1 S2				                     ; configure Z-probe endstop for low end on Z

M558 P8 C"!io0.in" H2.5 F360 T40000			 ; default to io0.in as z probe, will change in homing macros
G31 P500 X0 Y0 Z0

M950 F5 C"out5"								 ; create a system cooling fan (must be enabled during operation)

; Tools
M563 P0 D0 H1 F2                             ; define tool 0
G10 P0 X0 Y0 Z0                              ; set tool 0 axis offsets
G10 P0 R0 S0                                 ; set initial tool 0 active and standby temperatures to 0C

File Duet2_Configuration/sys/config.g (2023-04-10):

;Open5x_ver_20211118

; General preferences
G90                                         ; Send absolute coordinates...
M83                                         ; ...but relative extruder moves
M555 P2 						; Set firmware compatibility to look like Marlin

;Kinematics Profile for 5-axis (cartesian)
M669 K0 X1:0:0:0:0 Y0:-1:0:0:0 Z0:0:1:0:0 U0:0:0:1:0 V0:0:0:0:1

; Network
M550 P"Open5x"                        ; Set machine name
M552 S1                                     ; Enable network
;M552 S2                                     ; Enable AP


;*** Access point is configured manually via M587
M586 P0 S1                                  ; Enable HTTP
M586 P1 S0                                  ; Disable FTP
M586 P2 S0                                  ; Disable Telnet
M575 P1 S1 B57600			  ; Panel Due


; Drive Mappings
M569 P0 S0                                  ; Drive 1 goes backward: X Axis
M569 P1 S0                                  ; Drive 1 goes backwards: Y Axis
M569 P2 S0                                  ; Drive 2 goes backwards: Z Z Axis
M569 P3 S1                                  ; Drive 3 goes forwards: E0
M569 P4 S0                                  ; Drive 4 goes anti-clockwise: U Axis
M569 P5 S0				    ; Drive 5 goes anti-clockwise: V Axis


M584 X0 Y1 Z2 E3 U4 V5 ; My Driver Mapping

;Microstepping and Speed

M350 X16 Y16 Z16 E32 A16 B16 I1                 			; Configure microstepping with interpolation

M92 X100.00 Y100.00 Z400.00 E280.00 A26.667 B35.556 		    ; Set steps per mm and steps per degree
M566 X480.00 Y480.00 Z24.00 E270.00 A480.00 B480.00 P1     	    ; Set maximum instantaneous speed changes (mm/min)
M203 X12000.00 Y12000.00 Z750.00 E1500.00 A5000.00 B12000.00  	    ; Set maximum speeds (mm/min)
M201 X1000.00 Y1000.00 Z1000.00 E1000.00 A1000.00 B1000.00   	    ; Set accelerations (mm/s^2)
M906 X620.00 Y620.00 Z560.00 E700.00 A1300.00 B1300.00 I10            ; Set motor currents (mA) and motor idle factor in percent
M84 S30                                    			    ; Set idle timeout


;Axis Limit
M208 X-126:125   Y-92.3:50  Z125:-1 A-200:200 B-12000:12000					; Centre of the rotating bed is set to origin 0,0
M564 H0								; allow unhomed movement


; Endstops for each Axis
M574 X1 S3				 ; Set endstops controlled by motor load detection
M574 Y1 S3                               ; Set endstops controlled by motor load detection
M574 Z2 S4                               ; configure sensorless endstop for high end on Z (Detected by two motors)


; Stallgaurd Sensitivy
M915 X S3 F0 H400 R1		                ; Set X axis Sensitivity
M915 Y S3 F0 H400 R1		                ; Set y axis Sensitivity
M915 Z S3 F0 H400 R1		                ; Set z axis Sensitivity




; Z-Probe (manual)
M558 P0 H15 F120 T6000                          ; disable Z probe but set dive height, probe speed and travel speed


; Heatbed Heaters and Thermistor Bed 
M140 H-1 ; Disable heated bed

; Filament Sensor Port and Loading Feature ON
M950 J1 C"e0stop" ; Input 1 e0 Filament Sensor 
M581 P1 T2 S0 R0 ; Filament Sensor P1 triggers Trigger2.g always (R0)

; HotEnd Heaters and Thermistor HotEnd           
M308 S1 P"e0_temp" Y"thermistor" T100000 B4725 R4700  ; Set thermistor + ADC parameters for heater 1 HotEnd
M950 H1 C"e0heat" T1					; Create HotEnd Heater
M307 H1 A306.9 C115.4 D4.0 V23.8 B0		; Hotend PID Calibration and PWM
M143 H1 S285                            ; Set temperature limit for heater 1 to 285C HotEnd
M302 S185 R185

; Fans
M950 F1 C"Fan1" Q250				; Creates HOTEND Fan
M106 P1 T45 S255 H1                 ; HOTEND Fan Settings
M950 F0 C"Fan0" Q250				; Creates PARTS COOLING FAN
M106 P0 H-1                         ; Set fan 1 value, PWM signal inversion and frequency. Thermostatic control is turned off PARTS COOLING FAN

; Tools
M563 P0 D0 H1 F0                            ; Define tool 0 Heater Block 1
G10 P0 X0 Y0 Z0                             ; Set tool 0 axis offsets
G10 P0 R0 S0                                ; Set initial tool 0 active and standby temperatures to 0C

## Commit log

2022-10-27 strengthen u axis motor mount
    can be printed in-place without supports
    2 versions to support different length stepper shafts
    [U_axis_motor_mount_22.3mf, U_axis_motor_mount_22mm.step, U_axis_motor_mount_28mm.3mf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]
2022-10-29 3D printable V pulley
    Two version of an 80t pulley for the V axis, one optimized for printing in resin directly on the build plate, the other optimized for fdm.
    I will only be providing .step file going forward since they can be easily edited in CAD software and opened directly in PrusaSlicer for printing or exporting as .stl to open in other applications.
    [V_axis_pulley_80t_fdm.step, V_axis_pulley_80t_resin.step]
2022-10-30 Properly name file
    File should have been named 72t
    [V_axis_pulley_72t_fdm.step, V_axis_pulley_72t_resin.step]
2022-10-31 Update Materials_and_supplier.md
    Duet 3 mini 5+ and mini 2+ are Duet3D's recommended control solution.
2022-11-03 Strengthen V axis carrige
    The v axis has been reinforced and includes a mounting bracket for Duet CAN toolboards on the bottom. Supports both 4 & 6 bolt-pattern universal mounting hubs.
    [V_axis_carriage_4_bolt.step, V_axis_carriage_6_bolt.step, toolboard_23mm_bracket.step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]
2023-04-10 Update config.g
    Name of the U and V axis have now been changed to A&B to match the convention
    [config.g]
2023-04-17 import of voron assembly
2023-04-17 Rename Materials_and_supplier.md to 3D_Model/Prusa i3/Materials_and_supplier.md
2023-04-20 WIP - scripts/config for Duet Mini
    initial import of the necessary configuration and macros for the open5x voron
    [config.g, pause.g, resume.g]
2023-05-15 Initial rev for Jubilee 5-axis hardware
    [Left Bed Coupler.STL, Right Bed Coupler.STL, Z-axis Bridge Plate.STL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]
2024-03-31 upload of all new files
    [Open5x Assembly Oriented Print Parts.3mf, Toffsets.g, bed.g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]
